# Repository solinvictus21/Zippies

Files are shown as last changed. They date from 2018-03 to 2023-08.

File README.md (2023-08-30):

# Zippies

Zippies are a project developed to create tiny, open source robots capable of following predefined path routines at high velocity in tight coordination together.

Fully Assembled Zippy

This repository includes all the details you need to build and run a Zippy...

- A complete set of [3D models](BodyModels) created in [SketchUp](https://www.sketchup.com/) that are required to build the outer body of a Zippy. Each of these parts is intended to be printed on a 3D printer and has been exported to a set of [STL files](BodyModels/STL) for convenience.
- A [schematic](LighthouseCircuit) and [complete bill of materials]() for a circuit designed to sense IR signals from a single HTC Vive Lighthouse to enable highly accurate, sub-millimeter localized positioning and orientation. The circuit is built in [AutoDesk Eagle](https://www.autodesk.com/products/eagle/free-download) and the PCB is available for immediate purchase directly [from Osh Park]().
- A complete [list of the additional hardware required](Documentation/Hardware.md) to assemble a Zippy. 
- The [software](PlatformIO) required to enable your Zippy robot to follow any predefined path you wish to create. A sample path is included in the codebase for testing new Zippy builds.
- An [iPhone app](iOSClient) (work in progress) that will allow you to control the Zippy directly and aid in debugging over Bluetooth.
- A [path building app](Builder) (work in progress) using [Unity 3D]() designed to allow you to build and simulate routines for your Zippies to follow and, on supported platforms, allow you to upload them directly to the Zippy via Bluetooth LE for immediate testing.

See each of the links above for more details about each aspect of this project and feel free to contact me for any assistance you may need if you are interested in building your own Zippy.

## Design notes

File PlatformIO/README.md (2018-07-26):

# Zippies for TinyScreen+

The following is a BOM to build a Zippy...

1. 1x [TinyScreen+](https://tinycircuits.com/collections/processors/products/tinyscreenplus) Main processor board plus battery charger, battery connector, and 96x64 full-color OLED screen.
2. 1x [290mAh Lithium Ion Battery](https://tinycircuits.com/products/lithium-ion-polymer-battery-3-7v-290mah)
3. 2x [Micro Metal Gearmotors](https://www.pololu.com/product/2363) from Pololu.com.
4. 1x [Dual Motor Tinyshield](https://tinycircuits.com/products/dual-motor-tinyshield) to drive the motors.
5. 1x [Proto-Board Tinysheild](https://tinycircuits.com/collections/proto-boards/products/proto-board-tinyshield?variant=14984618887) Be sure to purchase the version with no top connector. It will get in the way of attaching the HTC Vive Lighthouse sensor circuit.
6. 1x [Bluetooth Low Energy Tinyshield](https://tinycircuits.com/collections/communication/products/bluetooth-low-energy-tinyshield) Optional. Provides communication with the iOS app, useful for debugging.

It's not a cheap project to start on. The above required components of the robot add up to ~$96, not including Bluetooth, and that's before the cost of a 3D printer and the tools required to solder together the circuit board for sensing the Lighthouse signal. This is admittedly not a project for the feint-hearted or anyone new to building robots, but it IS a project for anyone excited about doing something new.

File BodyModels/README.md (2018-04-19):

# Parts Required For Body Assembly

Nearly all parts required to build a Zippy are included in the 3D models in this repository, with a few minor additions noted below.

Body Parts

## 3D-Printed Items

The parts are all modeled using [SketchUp](https://www.sketchup.com/), inspected for 3D printing solidity with the [Solid Inspector² extension](https://extensions.sketchup.com/en/content/solid-inspector%C2%B2), and exported to STL files using [this excellent STL exporter extension](https://extensions.sketchup.com/en/content/sketchup-stl).

I then slice the STL files with [Ultimaker Cura](https://ultimaker.com/en/products/ultimaker-cura-software) and print them with ABS on a [Monoprice Select Mini V2](https://www.monoprice.com/product?p_id=21711) 3D printer, but other slicers, materials, and 3D printers should work just fine. I print all parts with a raft to prevent compression of the bottom layers of each part. You will likely need to adjust 3D print settings during slicing for some of the parts to ensure they print properly as noted for each part.

### Body Bottom (1x)

The container for the motors. It is separated from the rest of the body to ease the assembly process. Notable features include (1) a "pillow" on the bottom to prevent corners of the model from snagging on irregularities on the surface as it moves around, (2) annular snap fits on the top to attach it to the rest of the body, and (3) holes for the screws to firmly attach the motor.

I recommend printing this part with supports so that the bottom pillow forms cleanly, and after removing the raft and supports, finish the bottom with a bit of acetone to ensure a smooth surface.

### Body (1x)

The main/center portion of the body and the housing for the various circuit boards. Notable features include (1) four insets along the bottom to connect to the annular snap fits on the body bottom, (2) brackets inside near the front to keep the TinyScreen in place, (3) holes on the left side to allow access to the TinyScreen power switch and reset button, and (4) insets on the inside left and right to connect to the cantilever snap fits on the body top.

This part likely does not require printing with supports. The overhangs for the insets on the bottom are small enough that they should bridge perfectly fine during printing without supports.

### Body Top (1x)

As the name implies, this is the top that attaches to the body to fully enclose the Zippy. Notable features include (1) cantilever snap fits on either side to connect the body top to the body, (2) lugs on the back corners to ensure proper alignment with the body when attached, (3) two holes for the infrared sensors from the Lighthouse circuit, and (4) a hole for the USB port to allow reprogramming of the Zippy without requiring the top to be removed.

### Wheel Motor Gears (2x)

The gears which attach to the axles on the two motors. Note that the gear is actually modeled as a proper "involute gear" and that the center hole is D-shaped to ensure tight attachment to the motor axles.

I have been asked why I don't just attach the wheels directly to the motors and just let them be offset from each other on either side of the Zippy. That's a good question, and I did not do that for a good reason. The PID controllers in the software codebase used to control each wheel would have to account for the offset of each wheel from the diode sensors on the top of the Zippy, complicating the math required to do proper path-following. Having the wheels centered on either side eliminates this complexity, and...honestly...I think it just looks better this way.

### Wheels (2x)

The name is self-explanatory. The important thing to note about this part is that the axle of the wheel and the outer rim of the wheel must be printed together even though they are technically modeled as two separate parts. That's because the axle has two endcaps to hold the rim in place which are larger than the hole in the rim for the central rod of the axle, a rather ingenious idea that I stole from another wheel model I found while randomly browsing around Thingiverse. Once the part is printed and the raft is fully removed, the axle should be able to turn within the rim, allowing the wheel to rotate once attached to the body. I even recommend applying a small amount of a light oil-based lubricant to this part after it is printed and cleaned up, to ensure that the outer rim turns freely around the axle.

## Accessories

In addition to the 3D printed parts, you'll also require the following accessories to complete assembly.

- 4x [M1.6 x 3mm screws](https://www.amazon.com/gp/product/B071DXG8D4/ref=oh_aui_detailpage_o09_s00?ie=UTF8&psc=1) used to attach the motors firmly to the bottom of the body.
- 2x [5mm x 1.5mm O-Rings](https://www.amazon.com/gp/product/B0180EQC22/ref=oh_aui_search_detailpage?ie=UTF8&psc=1) used as the "tires" that attach to the 3D-printed wheels.

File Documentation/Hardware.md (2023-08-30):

# Zippy Parts

The following is a complete set of parts required to build and run a Zippy robot.

1. A full set of [3D printed body parts](../BodyModels)
2. 1x [TinyScreen+](https://tinycircuits.com/collections/processors/products/tinyscreenplus) Main processor board plus battery charger, battery connector, and 96x64 color OLED screen.
3. 1x [290mAh Lithium Ion Battery](https://tinycircuits.com/products/lithium-ion-polymer-battery-3-7v-290mah)
4. 1x [Dual Motor Tinyshield](https://tinycircuits.com/products/dual-motor-tinyshield)
5. 1x [Proto-Board Tinysheild](https://tinycircuits.com/collections/proto-boards/products/proto-board-tinyshield?variant=14984618887) Be sure to purchase the version with no top connector.
6. 1x [Bluetooth Low Energy Tinyshield](https://tinycircuits.com/collections/communication/products/bluetooth-low-energy-tinyshield)
7. 2x [Micro Metal Gearmotors](https://www.pololu.com/product/2363) from Pololu.com.
8. 1x [HTC Vive Lighthouse](https://www.vive.com/us/accessory/base-station)
9. 1x fully-assembled [Lighthouse Sensor Circuit](../LighthouseCircuit)

TODO
tires (O-rings)
male and female headers for connecting sensor circuit
wiring for connecting motors

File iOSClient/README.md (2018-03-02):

# iPhone Client for Zippies

Run this on your phone, and it will automatically find and connect to a nearby Zippy. It will eventually need an update to allow selecting which Zippy to connect to when multiple are found, but that's on the "to do" list and unlikely to be a short-term issue.

Note that the emulator does not support the Bluetooth Low Energy profile, so the app will only function on a real device, which means that you'll need a iPhone developer account ($100/year) to install it on your phone.

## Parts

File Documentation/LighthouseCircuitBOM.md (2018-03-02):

# Lighthouse Sensor Circuit

This circuit is designed to provide sensors that detect IR signals from the HTC Vive Lighthouse in order to provide localized positioning for the Zippy. The board layout is published on [Osh Park](https://oshpark.com/shared_projects/vZVPRIY6) for easy ordering. All you have to do is solder the components onto it. The BOM and links to Digikey components are provided below.

1. 2x [BP104-FASZ](https://www.digikey.com/product-detail/en/osram-opto-semiconductors-inc/BP-104-FAS-Z/475-1344-1-ND/1227850) These are the IR sensors, the eyes of the circuit
2. 1x [TLV2464ID](https://www.digikey.com/product-detail/en/texas-instruments/TLV2464ID/296-10608-5-ND/380874) The heart of the circuit: a fast and reliable quad op-amp from TI.
3. First phase: voltage divider.
  - 2x [27k resistors](https://www.digikey.com/product-detail/en/panasonic-electronic-components/ERJ-3EKF2702V/P27.0KHCT-ND/1746753)
  - 2x [100nF capacictors](https://www.digikey.com/product-detail/en/samsung-electro-mechanics/CL10B104JB8NNNC/1276-1033-1-ND/3889119)
4. Second phase: transimpedance amplification
  - 2x [2.2pF capacitcors](https://www.digikey.com/product-detail/en/samsung-electro-mechanics/CL10C2R2BB8NNNC/1276-1084-1-ND/3889170)
  - 4x [100k resistors](https://www.digikey.com/product-detail/en/panasonic-electronic-components/ERJ-PA3J104V/P100KBZCT-ND/5036238) Also used in fourth-phase inverting amplification.
5. Third phase: high-pass filter.
  - 2x [4.7nf capacitors](https://www.digikey.com/product-detail/en/samsung-electro-mechanics/CL10B472JB8NNNC/1276-2061-1-ND/3890147)
  - 2x [18k resistors](https://www.digikey.com/product-detail/en/panasonic-electronic-components/ERJ-3EKF1802V/P18.0KHCT-ND/1746738)
6. Fourth phase: inverting amplification
  - 2x [1k resistors](https://www.digikey.com/product-detail/en/panasonic-electronic-components/ERJ-PB3D1001V/P20283CT-ND/6214538)

The passives can be soldered onto the board in any orientation, but pay particular attention to the orientation of the op-amp and diodes. Schematic diagram follows below if you're not an Eagle user.

Lighthouse Sensor Schematic

This is essentially a mash-up and a doubling of the circuit I originally started with from [Alex Shtuchkin's project](https://github.com/ashtuchkin/vive-diy-position-sensor) and [another circuit](https://trmm.net/Lighthouse) tweeted about by Alan Yates along with [some lessons I've learned about op-amps](http://www.radio-electronics.com/info/circuits/opamp_non_inverting/op_amp_non-inverting.php) along the way and a LOT of experimentation. At this point, the circuit seems to be fairly reliable across the range of distances that I experiment with.

For the curious, it has been suggested that, if you only have one Lighthouse, you must have three sensors to determine orientation along a 2D plane. Not true, actually. To do it with only two sensors on a robot that does not move in the up/down direction (assuming your sensors are equally-spaced on either side of the robot like this one), then you can just cross the vector between the two sensors with the down vector (0,0,-1) to get the orientation.

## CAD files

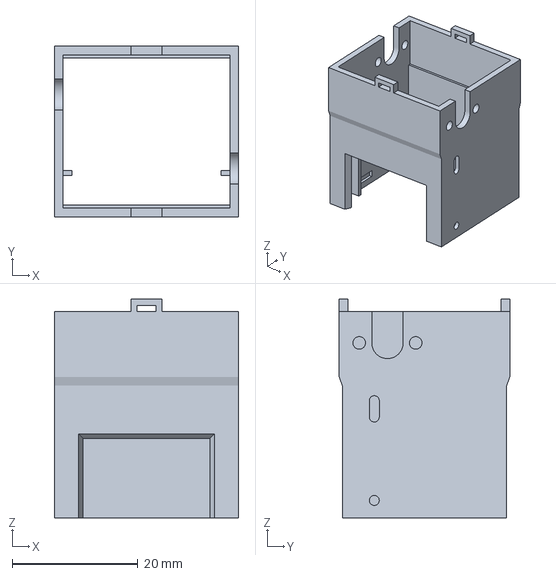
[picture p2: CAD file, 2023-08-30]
BodyModels/Body Middle - Experimental.3mf
29.4 x 27.2 x 34.9 mm

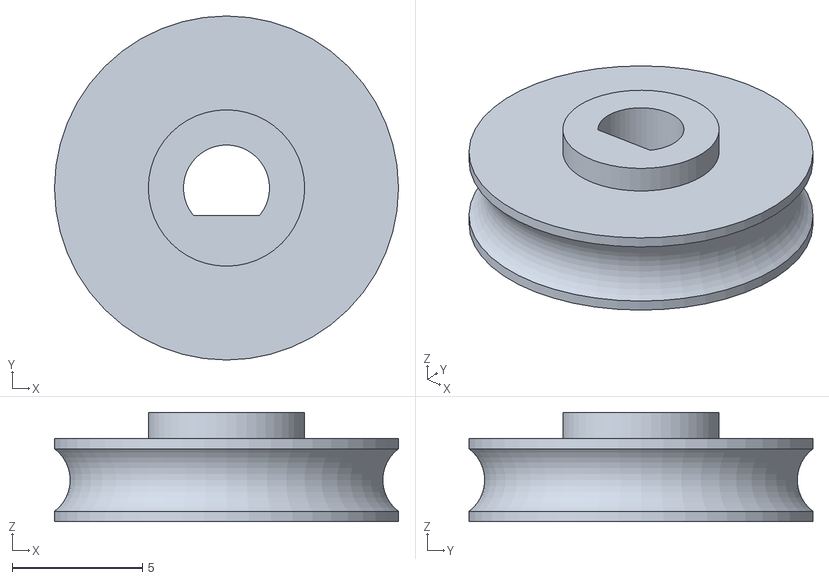
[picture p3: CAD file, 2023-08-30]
BodyModels/STL/Wheel.stl
13.2 x 13.2 x 4.20

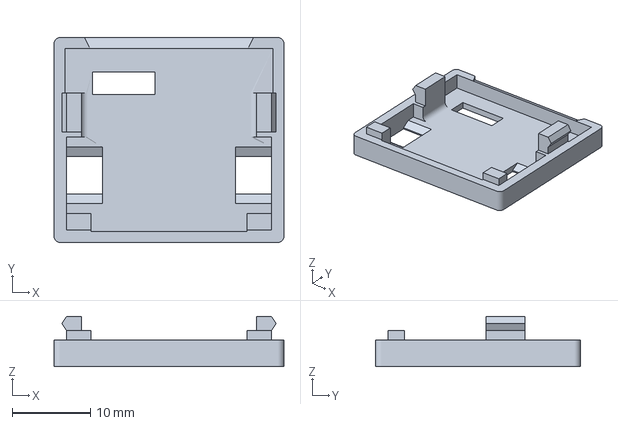
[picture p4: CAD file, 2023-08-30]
BodyModels/Body Top.3mf
29.4 x 26.2 x 6.40 mm

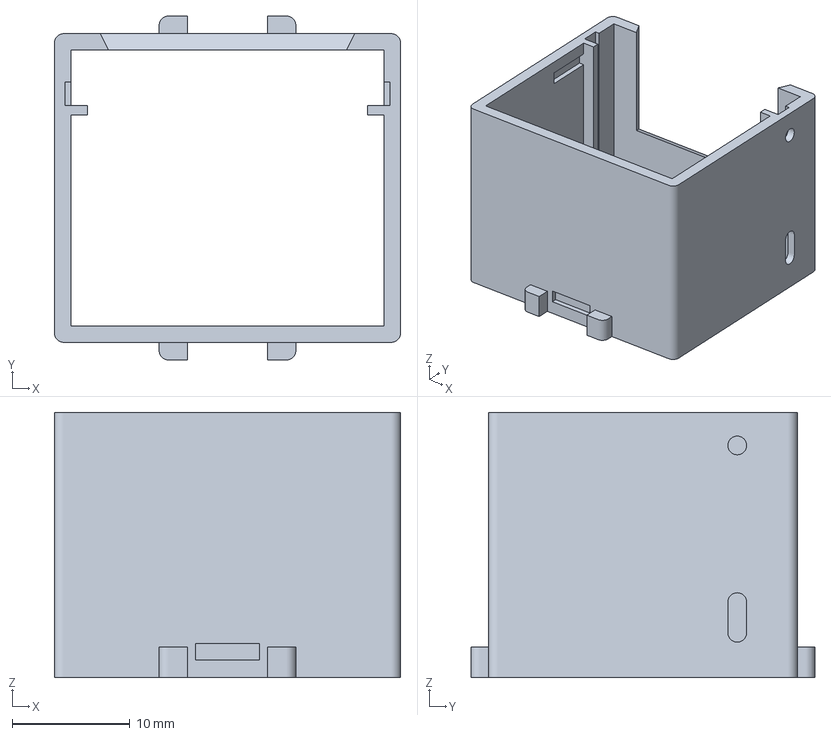
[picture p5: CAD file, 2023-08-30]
BodyModels/Body Middle.3mf
29.4 x 29.2 x 22.5 mm

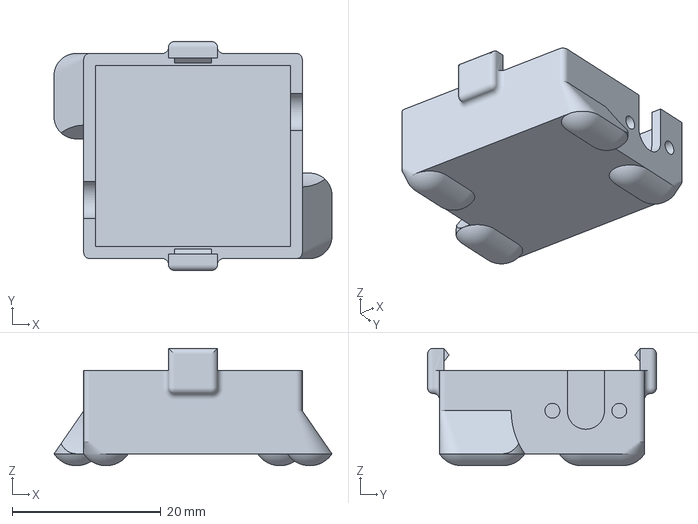
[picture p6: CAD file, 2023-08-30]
BodyModels/Body Bottom.3mf
37.4 x 30.8 x 15.8 mm

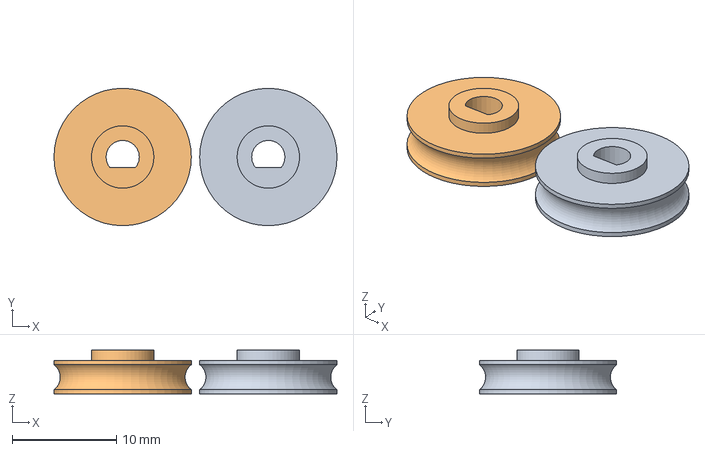
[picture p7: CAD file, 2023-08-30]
BodyModels/Wheels.3mf
27.2 x 13.2 x 4.20 mm

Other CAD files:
BodyModels/Body Parts.skp
BodyModels/Experimental Models.skp
BodyModels/Recharging Station.skp
BodyModels/STL/Body Bottom.stl
BodyModels/STL/Body Middle.stl
BodyModels/STL/Body Top.stl

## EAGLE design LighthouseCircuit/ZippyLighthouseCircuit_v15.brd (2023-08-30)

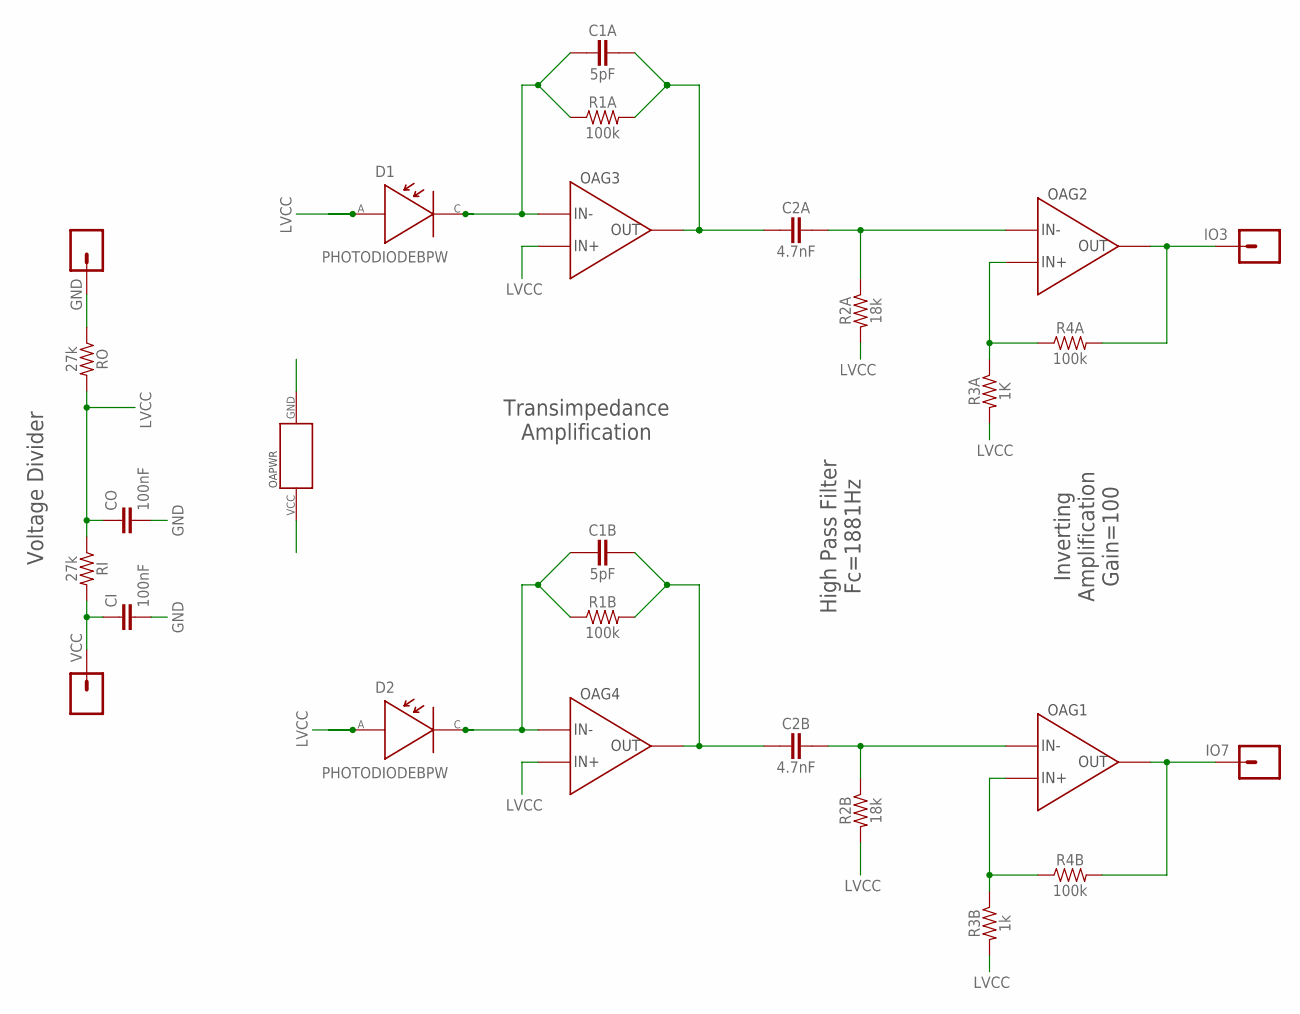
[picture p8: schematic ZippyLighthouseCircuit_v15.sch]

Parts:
C1A, C1B: 5pF; PASSIVE-0603
C2A, C2B: 4.7nF; PASSIVE-0603
CI: 100nF; 0603
CO: 100nF; 0603
D1, D2: PHOTODIODEBPW; BPW34_BP104_SMD
GND: CONN_01PTH_NO_SILK_YES_STOP; 1X01_NO_SILK
IO3, IO7: CONN_01PTH_NO_SILK_YES_STOP; 1X01_NO_SILK
OA: TLV2464IDM; D14-M
R1A, R1B, R4A, R4B: 100k; PASSIVE-0603
R2A, R2B: 18k; PASSIVE-0603
R3A: 1K; PASSIVE-0603
R3B: 1k; PASSIVE-0603
RI: 27k; 0603
RO: 27k; 0603
VCC: CONN_01PTH_NO_SILK_YES_STOP; 1X01_NO_SILK

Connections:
D1IN: C1B.1, D2.CATHODE, OA.13 (IN-), R1B.1
D1OA2P: C2B.2, OA.2 (IN-), R2B.1
D1OAOUT1: C1B.2, C2B.1, OA.14 (OUT), R1B.2
D2IN: C1A.1, D1.CATHODE, OA.9 (IN-), R1A.1
D2OA1OUT: C1A.2, C2A.1, OA.8 (OUT), R1A.2
D2OA2N: OA.5 (IN+), R3A.1, R4A.1
D2OA2P: C2A.2, OA.6 (IN-), R2A.1
GND: CI.2, CO.2, GND.1, OA.11 (GND), RO.1
IO3: IO3.1, OA.7 (OUT), R4A.2
IO7: IO7.1, OA.1 (OUT), R4B.2
LVCC: CO.1, D1.ANODE, D2.ANODE, OA.10 (IN+), OA.12 (IN+), R2A.2, R2B.2, R3A.2, R3B.2, RI.1, RO.2
unnamed: OA.3 (IN+), R3B.1, R4B.1
VCC: CI.1, OA.4 (VCC), RI.2, VCC.1

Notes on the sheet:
Voltage Divider
High Pass Filter Fc=1881Hz
Transimpedance Amplification
Inverting Amplification Gain=100

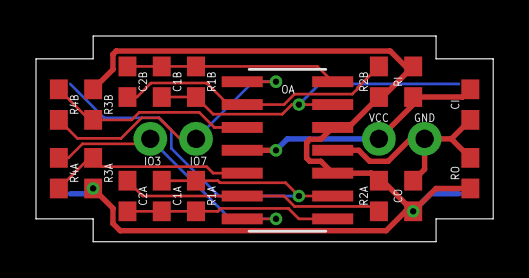
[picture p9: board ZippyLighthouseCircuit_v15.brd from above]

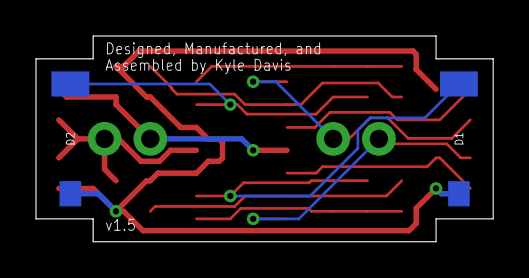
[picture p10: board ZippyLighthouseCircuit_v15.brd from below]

Board: 2 copper layers, 25.4 x 11.4 mm, 23 parts (2 on the bottom side), 13 nets.

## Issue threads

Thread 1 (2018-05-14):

Some questions.

modulab, 2018-05-14:
Hi,
I have't got the hardware yet but i'm planing to. I have a few questions for you.
Why did you use this MCU? Have you researched other options too?
How precise is the positioning at 48Mhz?
What is the current speed of the robot?
Awesome work !

solinvictus21, 2018-05-15:
Edit: Second attempt. My first attempt to respond to your email with an
attached video showing the speed of the Zippy moving about on the floor
failed because your email server rejected it for size. I'll try to get the
video uploaded to YouTube as additional info, but resending the rest of the
email without the attachment for now...

Hi! You are the first person to express interest in building a Zippy, so I
definitely want to help you in any way I can. To answer your questions in
short form, (a) it was just the fastest path to my end goal, (b) lots of
them, but I have research many options and am always looking for more, (c)
less than half a mm at distances of 1-5 meters from the Lighthouse, and (d)
about 600-800mm/sec. The lower speed during turns and the faster on
straightaways. I attached a relevant video to show him in motion.

For the longer answers, I've provided more detail below...

(a) I used this MCU strictly because it appeared to be the fastest path to
my goal, but I'm open to suggestions for other MCUs. While I was
experimenting with the Lighthouse sensor circuit, I actually implemented
early versions of the software first on the Arduino Uno and then the Teensy
3.2 platform. Based on your question, I'm guessing you're probably already
aware that there are basically two categories of MCUs: 8-bit and 32-bit.
And the latter is obviously significantly more capable than the former. I'm
a software developer by trade, and I actually didn't realize when I started
this project that there was such a big performance gap in the choice of
MCUs for robotics projects. I've since begun to favor Cortex-based
processors (although ESP32 is an interesting platform as well, mostly for
the WiFi integration), and the SAMD21-G18A variant built into the
TinyScreen+ was able to provide timings that matched up with the research
I've done to understand the timings of the Lighthouse..

(b) I've researched LOTS of other options, but I'm always open to others.
Caveat: I'm not a hardware engineer. I've only learned how to solder by
hand down to about 50 mils, which limits my ability to design circuit
boards using components that I'd otherwise prefer to integrate together
into a custom PCB for this project.

(c) I actually have a related codebase that I use to research exactly this
question, and all testing I've done is based on that codebase. If you build
one (and I'll put together some YouTube assembly videos to help if you do),
then you will be able to confirm the same data.

(d) The iPhone app that integrates with the Bluetooth connection will
display the information confirming these speeds as well. I'm still tuning
the PID controllers, though, so I may be able to get significantly faster
speeds in the future as well.

Just let me know if you have any more questions.

Kyle

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

solinvictus21, 2018-05-15:
YouTube video of one moving around a predefined path on the floor based on
positioning info from the Lighthouse.

https://www.youtube.com/edit?o=U&video_id=sSDTUJjHLLc

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

lgbeno, 2018-05-15:
Hey Kyle & Modulab,

Cool discussion here, glad to see interest in this area!  I can chime in a little bit on MCU selection because I've researched it quite a lot and have implemented the low level lighthouse stuff on a few MCUs (SAMD21 included).

I would say that SAMD21 is a pretty good choice for this application.  Mostly because the Arduino support is excellent and that makes adaptation easier for a larger population of people.  Most important to the application is availability of a >=24bit or larger timer capture that can be clocked at 48MHz or higher.  SAMD21 has this!  It is the most difficult processor by far to configure the timer properly but Kyle, looks like you have already gone through that pain.

Other processors that I've used are ST STM32F415 and NXP 54114.  The main reason for jumping to a chip like this is to get a faster clock rate and hardware floating point but in the process, you sacrifice the convenience of Arduino.

STM32F415 is quite the beast but also much more costly and physically much larger than the other options.

I think that the Teensy processors are also capable of hardware pulse capture so they are probably the best compromise of a faster ARM processor that also includes Floating point and is very maker friendly.

With that said I think SAMD21 is still an excellent choice with all things considered.

Unfortunately ESP8266 does not seem to have the proper timer capture functionality, some other peripherals can be hacked to serve the function but require constant CPU intervention.  I have not researched ESP32 in length but I think that it is very similar in this regard.

With a lot of research, I can say that I have yet to find a Radio System on Chip supporting all of these requirements which is unfortunate.

-Luke

solinvictus21, 2018-05-16:
> ... but Kyle, looks like you have already gone through that pain.

And indeed, it was painful. :) Programming at the AVR layer instead of using the Arduino APIs required reading and understanding a lot of different sections of the SAMD21 datasheet and a LOT of trial-and-error, but it's working great now. Still some optimizations I'd like to eventually add, such as using DMA to collect the pulse edge timing instead of software interrupts, and there seems to be some drift DFLL clock in the SAMD21 that I want to figure out how to tighten up. But before I tackle those, I want to make sure that SAMD21 is the platform I'll be sticking with for a while, particularly since ESP32 has caught my eye.

I actually started with Teensy 3.2, and I have quite a bit of the AVR-level code written to capture the Lighthouse edges on that platform as well, but it's not currently checked into the GitHub repository because the codebase on the whole is really quite stale at this point compared to the TinyScreen codebase. It wouldn't take much to move back in the future if I decided to go there again.

I figured the ESP8266 (and ATMega328P in the original Arduino) was probably too under-powered to get perform timings at the level that one needs for Lighthouse processing. I actually did some initial experimentation on the original Arduino before discovering this, though when I last looked back at it, I managed to home in on better timings than I would have expected for the processor speed it has available. Still, it eventually become another version of the codebase that has since been abandoned for exactly the reasons you describe.

But as far as the ESP32 platform, I understand that it actually quite capable and is comparable to (or even better than) the leap from the ATMega328P to SAMD21 in terms of sheer processing power. I am drawn to it as a possibility simply for the possibility of replacing the Bluetooth communication I'm currently doing, which is really only point-to-point, for the WiFi capabilities built into the ESP32 platform, which would allow me to do broadcast communication via UDP packets. That's something I will eventually need as I move toward trying to get multiple Zippies to move around in tight coordination together.

If I stick with SAMD21 instead of moving to ESP32, I'll also have to figure out the radio-system-on-a-chip issue(nrf24l01 currently has my eye) as well as how to hand solder down to smaller sizes, since they're all pretty tiny. Sounds like you have some good experience with this stuff, if you have any insight into how to make soldering tinier components easier, I'm all ears. :)

Regards,
Kyle

lgbeno, 2018-05-17:
Haha, yes, sorry I needed to laugh out loud about the timer stuff because it is almost not documented at all in the datasheet.  You probably used some Arduino forum reference code from some very nice people who also helped me read between the lines of those documents!

The DMA work was significantly and I have some ref code for that.  I based it off of an ADC example and now that you understand the event system better, this is just an extension of that knowledge.
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
solinvictus21, 2018-05-19:
@modulab

Sorry about the faulty YouTube link. This one should work for you…

https://www.youtube.com/watch?v=sSDTUJjHLLc

I just caught up on your post. You are in *exactly* the same place I was several months back. I am more than happy to help you out.

First of all, let me start by saying that I’m ultimately developing a “swarm” platform as well. I want to get to the point that I can build several Zippies that can do their own independent path-following while knowing exactly where they are and avoiding each other. To accomplish this, there is definitely a lot more to consider besides just the MCU. Specifically, you’ll need 4 additional pieces of functionality to think about when choosing a platform: battery recharging, wireless communication, motor drivers, and lighthouse sensors. Whichever platform you choose, you will also need to solve those 4 other problems to build out a swarm platform. Please take a couple of pieces of advice from the knowledge I gained from many months of failures I experienced at the beginning of this project.

- Use a 3D printer to make your robot body. This has been endlessly useful in allowing me to iterate on design changes quickly. I can provide recommendations for inexpensive 3D printers if you want them.

- Use metal gear motors, at least while you’re in the initial stages of building out the software. Un-geared DC motors have such a low torque and high RPM that error rates in movement are a nightmare. Plastic gear motors just end up in the garbage every few weeks. The extra space required for metal gear motors is worth the payoff in reliability and movement consistency. I recommend the gear motors I’m currently using for Zippies for a reliable motor that has consistent movement, but whatever motors you choose, stick with something between 500-2000RPM. No faster. You can always move to smaller and/or faster motors later. Of course, stepper motors and continuous servo motors are an option as well, but those are much slower, much larger, and are designed to provide a kind of closed-loop control that you are trying to implement using the Lighthouse instead, so why bother?

If you’re building out your own PCB, which it sounds like you might be doing, I highly recommend the SAMD21. It has a timer clock that you can use that is 48MHz, which is exactly the same as the timer clock in the Lighthouse. Plus it has the ability to capture timings in hardware, which is much more accurate compared to trying to capture timings based on a software interrupt. Timing is crucial when a handful of clock ticks can result in a difference of several centimeters in your estimated position. And if you choose the SAMD21, I will be able to provide better guidance with code samples and such while you’re trying to build the software to calculate position. Regardless of which platform you choose, though, let me know how your project progresses, and I’ll be more than happy to assist with any info that I can, since it sounds like we’re both pursuing a similar path.

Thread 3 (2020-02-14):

Having trouble to get the board to run error: "Ignoring signal echo: 5410 13563 26 5464 24463"

bbroecker, 2020-02-14:
Hi @solinvictus21,

I really like your project and I tried to make it run, but I'm running into problems.
I build the board with the specifications (resistors/capasitors) mentioned on the Readme.md from the
feature/MovementPlanningSupport branch.
The SensorFusor::loop always returns false,

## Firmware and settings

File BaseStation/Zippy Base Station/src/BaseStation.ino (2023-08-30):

#include "zippies/basestation/BaseStationController.h"

BaseStationController baseStationController;

void setup()
{
  SerialUSB.begin(115200);
  while (!SerialUSB);
  SerialUSB.println("Started serial communication.");

  baseStationController.start();
}

void loop()
{
  baseStationController.loop();
}

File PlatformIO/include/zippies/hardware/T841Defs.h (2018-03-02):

/*
T841Defs.h - Last modified 30 July 2015

These are register definitions for the ATTiny841, generated from files
included in the AVR-GCC project.

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
Written by Ben Rose for TinyCircuits.

The latest version of this library can be found at https://tiny-circuits.com/
*/

//Registers and associated bit numbers

#define T841_ADCSRB  0x20+0x04
#define T841_ADTS0   0
#define T841_ADTS1   1
#define T841_ADTS2   2
#define T841_ADLAR   3

#define T841_ADCSRA  0x20+0x05
#define T841_ADPS0   0
#define T841_ADPS1   1
#define T841_ADPS2   2
#define T841_ADIE    3
#define T841_ADIF    4
#define T841_ADATE   5
#define T841_ADSC    6
#define T841_ADEN    7

#define T841_ADCL    0x20+0x06
#define T841_ADCH    0x20+0x07

#define T841_ADMUXB  0x20+0x08
#define T841_GSEL0   0
#define T841_GSEL1   1
#define T841_REFS0   5
#define T841_REFS1   6
#define T841_REFS2   7

#define T841_ADMUXA  0x20+0x09
#define T841_MUX0    0
#define T841_MUX1    1
#define T841_MUX2    2
#define T841_MUX3    3
#define T841_MUX4    4
#define T841_MUX5    5

#define T841_ACSR0A  0x20+0x0A
#define T841_ACIS00  0
#define T841_ACIS01  1
#define T841_ACIC0   2
#define T841_ACIE0   3
#define T841_ACI0    4
#define T841_ACO0    5
#define T841_ACPMUX2 6
#define T841_ACD0    7

#define T841_ACSR0B  0x20+0x0B
#define T841_ACPMUX0 0
#define T841_ACPMUX1 1
#define T841_ACNMUX0 2
#define T841_ACNMUX1 3
#define T841_ACOE0   4
#define T841_HLEV0   6
#define T841_HSEL0   7

#define T841_ACSR1A  0x20+0x0C
#define T841_ACIS10  0
#define T841_ACIS11  1
#define T841_ACIC1   2
#define T841_ACIE1   3
#define T841_ACI1    4
#define T841_ACO1    5
#define T841_ACBG1   6
#define T841_ACD1    7

#define T841_ACSR1B  0x20+0x0D
#define T841_ACME1   2
#define T841_ACOE1   4
#define T841_HLEV1   6
#define T841_HSEL1   7

#define T841_TIFR1   0x20+0x0E
#define T841_TOV1    0
#define T841_OCF1A   1
#define T841_OCF1B   2
#define T841_ICF1    5

#define T841_TIMSK1  0x20+0x0F
#define T841_TOIE1   0
#define T841_OCIE1A  1
#define T841_OCIE1B  2
#define T841_ICIE1   5

#define T841_TIFR2   0x20+0x10
#define T841_TOV2    0
#define T841_OCF2A   1
#define T841_OCF2B   2
#define T841_ICF2    5

#define T841_TIMSK2  0x20+0x11
#define T841_TOIE2   0
#define T841_OCIE2A  1
#define T841_OCIE2B  2
#define T841_ICIE2   5

#define T841_PCMSK0  0x20+0x12

#define T841_GPIOR0  0x20+0x13

#define T841_GPIOR1  0x20+0x14

#define T841_GPIOR2  0x20+0x15

#define T841_PINB    0x20+0x16
#define T841_PINB3   3
#define T841_PINB2   2
#define T841_PINB1   1
#define T841_PINB0   0

#define T841_DDRB    0x20+0x17
#define T841_DDRB3   3
#define T841_DDRB2   2
#define T841_DDRB1   1
#define T841_DDRB0   0

#define T841_PORTB   0x20+0x18
#define T841_PORTB3  3
#define T841_PORTB2  2
#define T841_PORTB1  1
#define T841_PORTB0  0

#define T841_PINA    0x20+0x19
#define T841_PINA7   7
#define T841_PINA6   6
#define T841_PINA5   5
#define T841_PINA4   4
#define T841_PINA3   3
#define T841_PINA2   2
#define T841_PINA1   1
#define T841_PINA0   0

#define T841_DDRA    0x20+0x1A
#define T841_DDRA7   7
#define T841_DDRA6   6
#define T841_DDRA5   5
#define T841_DDRA4   4
#define T841_DDRA3   3
#define T841_DDRA2   2
#define T841_DDRA1   1
#define T841_DDRA0   0

#define T841_PORTA   0x20+0x1B
#define T841_PORTA7  7
#define T841_PORTA6  6
#define T841_PORTA5  5
#define T841_PORTA4  4
#define T841_PORTA3  3
#define T841_PORTA2  2
#define T841_PORTA1  1
#define T841_PORTA0  0

#define T841_EECR    0x20+0x1C
#define T841_EERE    0
#define T841_EEPE    1
#define T841_EEMPE   2
#define T841_EERIE   3
#define T841_EEPM0   4
#define T841_EEPM1   5

#define T841_EEDR    0x20+0x1D

#define T841_EEARL   0x20+0x1E
#define T841_EEARH   0x20+0x1F

#define T841_PCMSK1  0x20+0x20

#define T841_WDTCSR  0x20+0x21
#define T841_WDE     3
#define T841_WDP0    0
#define T841_WDP1    1
#define T841_WDP2    2
#define T841_WDP3    5
#define T841_WDIE    6
#define T841_WDIF    7

#define T841_TCCR1C  0x20+0x22
#define T841_FOC1B   6
#define T841_FOC1A   7

#define T841_GTCCR   0x20+0x23
#define T841_PSR     0
#define T841_TSM     7

#define T841_ICR1L   0x20+0x24
#define T841_ICR1H   0x20+0x25

// Reserved [0x26..0x27]

#define T841_OCR1BL  0x20+0x28
#define T841_OCR1BH  0x20+0x29

#define T841_OCR1AL  0x20+0x2A
#define T841_OCR1AH  0x20+0x2B

#define T841_TCNT1L  0x20+0x2C
#define T841_TCNT1H  0x20+0x2D

#define T841_TCCR1B  0x20+0x2E
#define T841_CS10    0
#define T841_CS11    1
#define T841_CS12    2
#define T841_WGM12   3
#define T841_WGM13   4
#define T841_ICES1   6
#define T841_ICNC1   7

#define T841_TCCR1A  0x20+0x2F
#define T841_WGM10   0
#define T841_WGM11   1
#define T841_COM1B0  4
#define T841_COM1B1  5
#define T841_COM1A0  6
#define T841_COM1A1  7

#define T841_TCCR0A  0x20+0x30
#define T841_WGM00   0
#define T841_WGM01   1
#define T841_COM0B0  4
#define T841_COM0B1  5
#define T841_COM0A0  6
#define T841_COM0A1  7

// Reserved [0x31]

#define T841_TCNT0   0x20+0x32
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

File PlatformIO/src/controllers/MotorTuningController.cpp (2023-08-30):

#include "zippies/controllers/MotorTuningController.h"
#include "zippies/config/BodyConfig.h"

#define DEFAULT_TEST_TIME 1000
#define DEFAULT_MOTOR_POWER_DELTA 100.0
#define DEFAULT_ACCEPT_STRAIGHT_MOTION 200.0
// #define TEST_START_MOTOR_LEFT 7200.0
// #define TEST_START_MOTOR_RIGHT 9100.0
#define TEST_START_MOTOR_LEFT 6800.0
#define TEST_START_MOTOR_RIGHT 8800.0
#define TEST_SLOW_MOTION_THRESHOLD 100.0
#define EPSILON_LINEAR 1.0
#define EPSILON_ANGULAR 0.052359877559830

//power differential on orange is 9143 and 7156 = 0.121909319590159

MotorTuningController::MotorTuningController(SensorFusor* s)
  : sensors(s)
{
    leftMotorPower = TEST_START_MOTOR_LEFT;
    rightMotorPower = TEST_START_MOTOR_RIGHT;
}

void MotorTuningController::resetTest()
{
    testStartingPosition.set(sensors->getPosition());
    motors.setMotorsDirect(leftMotorPower, rightMotorPower);
    testTimer = DEFAULT_TEST_TIME;
}

void MotorTuningController::start()
{
    deltaPosition.reset();
    linearVelocity = 0.0;
    turnRadius = 0.0;
    powerDifferential = 0.0;
    testComplete = false;
    resetTest();

    display.clearScreen();
    displayMetrics();
    display.displayText(0, 5 * display.getFontHeight(), "STARTED");
}

bool MotorTuningController::loop(unsigned long deltaTime)
{
    if (testComplete)
        return true;

    if (deltaTime < testTimer) {
        testTimer -= deltaTime;
        return true;
    }
    testTimer = DEFAULT_TEST_TIME;
    display.displayText(0, 5 * display.getFontHeight(), "TESTING");

    //evaluate our motion during the previous test
    calculateMetrics();
    displayMetrics();

    if (ensureTestableMotion()) {
        switch(currentTestState) {
            case MotorTuningTestState::PowerDifferential:
                testPowerDifferential();
                break;
            case MotorTuningTestState::Stiction:
                testStiction();
                break;
            case MotorTuningTestState::MinimumStraightSpeed:
                testMinimumStraightSpeed();
                break;
        }
    }

    return true;
}

bool MotorTuningController::ensureTestableMotion()
{
    //check if we're in motion
    if (deltaPosition.position.getD() < EPSILON_LINEAR) {
        //we're not moving at all; ramp up the power on both wheels
        leftMotorPower += DEFAULT_MOTOR_POWER_DELTA;
        rightMotorPower += DEFAULT_MOTOR_POWER_DELTA;
        resetTest();
        return false;
    }

    //check if we're turning
    double turn = deltaPosition.orientation.get();
    if (fabs(turn) >= EPSILON_ANGULAR) {
        //attempt to straighten our motion
        double powerDifference = 2.0 * powerDifferential * (leftMotorPower + rightMotorPower);
        leftMotorPower -= powerDifference;
        rightMotorPower += powerDifference;
        resetTest();
        return false;
    }

    return true;
}

void MotorTuningController::testPowerDifferential()
{
    //continue moving long enough to prove that we're moving straight
    if (deltaPosition.position.getD() > DEFAULT_ACCEPT_STRAIGHT_MOTION) {
        motors.stopMotors();
        testComplete = true;
        display.displayText(0, 5 * display.getFontHeight(), "DIFF DONE");
    }
}

void MotorTuningController::testStiction()
{
    //now that we're moving straight, test how slow we can go
    if (deltaPosition.position.getD() > TEST_SLOW_MOTION_THRESHOLD) {
        leftMotorPower -= 5.0 * DEFAULT_MOTOR_POWER_DELTA;
        rightMotorPower -= 5.0 * DEFAULT_MOTOR_POWER_DELTA;
        resetTest();
        return;
    }

    motors.stopMotors();
    testComplete = true;
    display.displayText(0, 5 * display.getFontHeight(), "STIC DONE");
}

void MotorTuningController::testMinimumStraightSpeed()
{
}

void MotorTuningController::calculateMetrics()
{
    const ZMatrix2* currentPosition = sensors->getPosition();
    deltaPosition.set(currentPosition);
    deltaPosition.unconcatFrom(&testStartingPosition);

    double angularVelocity = deltaPosition.position.atan();
    if (angularVelocity == 0.0) {
        linearVelocity = deltaPosition.position.getY();
        turnRadius = 0.0;
        return;
    }

    linearVelocity =
        (deltaPosition.position.getD() * angularVelocity) /
        sin(angularVelocity);
    turnRadius = linearVelocity / angularVelocity;

    powerDifferential = 1.0 -
            ((fabs(turnRadius) - WHEEL_CENTER_BODY_CENTER_OFFSET) /
            (fabs(turnRadius) + WHEEL_CENTER_BODY_CENTER_OFFSET));
    if (turnRadius < 0.0)
        powerDifferential = -powerDifferential;
}

void MotorTuningController::displayMetrics()
{
    uint8_t y = 0;
    display.displayLabelAndData(0, 0, "R", (int)rightMotorPower);
    display.displayLabelAndData(SCREEN_WIDTH_PIXELS_2, 0, "L", (int)leftMotorPower);

    y += display.getFontHeight();
    display.displayLabelAndData(0, y, "D", deltaPosition.position.getD());
    display.displayLabelAndData(SCREEN_WIDTH_PIXELS_2, y, "O", RAD2DEG * deltaPosition.orientation.get());

    y += display.getFontHeight();
    display.displayLabelAndData(0, y, "V", (int)linearVelocity);
    display.displayLabelAndData(SCREEN_WIDTH_PIXELS_2, y, "R", (int)turnRadius);

    y += display.getFontHeight();
    display.displayLabelAndData(0, y, "P", 100.0 * powerDifferential);
}

void MotorTuningController::stop()
{
    motors.stopMotors();
    if (!testComplete)
        display.displayText(0, 5 * display.getFontHeight(), "STOPPED");
}

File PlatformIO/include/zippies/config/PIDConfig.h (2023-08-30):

#ifndef _PIDCONFIG_H_
#define _PIDCONFIG_H_

#define PID_OUTPUT_LIMIT                   60000.0

//PID CONFIGURATION
#define PID_KP                               300.0
#define PID_KI                                 0.0
#define PID_KD                                22.0

#endif

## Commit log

2018-03-02 Added 3D models for body assembly.
    [Body Bottom.skp, Body Top.skp, Body.skp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]
2018-03-02 Added schematic and board layout for HTC Vive Lighthouse circuit.
    [Horizontally_Mounted_Lighthouse.brd, Horizontally_Mounted_Lighthouse.sch]
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2018-03-05 Renamed Arduino project to remove '+' symbol. Updated PID controller to be a little more accurate.
    [Horizontally_Mounted_Lighthouse.brd, Horizontally_Mounted_Lighthouse.sch]
2018-04-04 Preparing for minor Lighthouse tracking refactor.
    [ExenMiniShield.brd, ExenMiniShield.sch]
2018-04-18 Now have a working PID model. Refactoring MoveTowardPoint into FollowPath to accept multiple points.
2018-04-19 Finally got the PID control ironed out. They will now smoothly follow a demo elliptical path in area of about 2 meters across and 1.5 meters in depth all on their own.
    [ExenMiniShield.brd]
2018-05-04 Modified 3D body models to use offset, direct-drive wheels because the gears were too small to be printed accurately enough to prevent binding and other movement errors that prevented accurate self-n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
    [ExenMiniShield.brd]
2018-05-08 As the self-driving control model has become more refined, I've been able to push the Zippies faster. Now set at a max velocity of 800mm/s.
2018-05-09 Further refined the driving model and improved the position data by incorporating factory calibration data into the position calculation based on code and documentation from the libsurvive project. T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
2018-05-24 Significantly stabilized the acceleration from full stop by slowing down the maximum speed. There is a physical limitation preventing them from accelerating any faster from full stop. Now that their 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
    [ExenMiniBatteryShield.brd, ExenMiniBatteryShield.sch, ExenMiniShield.brd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]
2018-05-30 Moved to separate PID configuration for each wheel. Since the left wheel is offset toward the rear and the right wheel is offset toward the front, the left wheel needs to be less aggressive or the Zi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
    [ExenMiniLighthouseShield.brd, ExenMiniLighthouseShield.sch, ExenMiniMotorShield.brd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]
2018-07-12 Reached a point where auto-drive mode is consistent and reliable.
    [Body Bottom.skp, Body Top.skp, Body.skp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]
2018-07-26 Path following is now very smooth. Zippies sync up on Lighthouse OOTX frame preamble (17 successive zero OOTX bits). Added config to modify behavior of different Zippies. Started work on using Blueto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
    [Body Bottom.skp]
2018-08-01 Zippies can now perform perfectly synchronous drive along any predefined path.
    [Body Bottom.skp, ExenMiniLighthouseShield.sch, ExenMiniShield.brd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]
2018-08-16 Tagged model in each SketckUp file that should be used as the current model to 3D print.
    [Body Bottom.skp, Body Top.skp, Body.skp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]
2018-08-17 Added an integrated motor/lighthouse circuit design and updated path following code to use bezier curves to make path following significantly smoother.
    [CenteredLighthouseCircuit.brd, CenteredLighthouseCircuit.sch, DiodeBoard.brd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]
2018-08-28 Working on creating individual commands and implementing arbitrary path-following of straight line segments as well as bezier curves.
    [MainBoard.brd, MainBoard.sch, RadioShield.brd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]
2018-10-02 Beginning to transition PID model from linear+angular velocity PIDs to independent PIDs for each wheel.
    [Body Bottom.skp, Body Top.skp, Body.skp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]
2018-11-08 Implemented two different models for kinematics. Experimenting with each to determine which is more reliable across the widest range of velocities.
    [Body Bottom.skp, Body Top.skp, Wheel.skp]
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2019-03-01 Significantly stabilized the position calculation and the new driving model with independent PIDs for each wheel.
    [Body Bottom.skp, Body Top.skp, Body.skp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]
2019-04-19 Progress toward using bi-arc computations for execution of path following.
    [Body Bottom.skp, Body Top.skp, Body.skp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]
2019-06-18 Added support for bi-arc movement, which can be more easily linearly interpolated than cubic bezier movement. Made several other architectural changes to streamline movement planning.
    [Body Top.skp, Body.skp, Wheel.skp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]
2019-06-27 Minor changed to SketchUp models.
    [Body Top.skp, Wheel.skp]
2019-08-23 Numerous improvements to movement algorithm, path planning, and dance routine execution.
    [Body Top.skp, Body.skp]
2019-11-01 Significantly refactored the sensor fusion to calculate updated positions in lock-step with the Lighthouse sweeps. New positions are now calculated only after both sensors have received a hit on both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
2019-11-26 Eliminated use of routine controller and simplified the model for defining paths while adding support for velocity easing for each path segment.
2019-12-27 Working on initial demo of multiple Zippies in coordination.
    [ExenMiniBatteryShield.brd, ExenMiniBatteryShield.sch, ExenMiniLighthouseShield.brd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]
2020-02-01 Made some huge strides in these changes. Nothing is quite as satisfying as deleting code, and I've deleted much code in this commit, because I've been able to develop a new path-following algorithm t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
    [Recharging Station.skp]
2020-04-08 Significant changes and refactored codebase layout. Improvements made to path following, PID control, path execution, added a new default path, and many other changes.
    [Body Bottom.skp, Body Parts.skp, Body Top.skp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]
2020-07-02 Switched path definitions to use monotonic hermite curves, allowing for significantly more sophisticated and flexible path planning.
    [Body Bottom.stl, Body Middle.stl, Body Parts.skp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]
2020-07-22 Working on a new path following implementation.
    [Body Bottom.3mf, Body Middle - Experimental.3mf, Body Middle.3mf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]
2020-12-09 Attempting to perfect path following controller code. Preparing to delete old path definition code.
    [Body Middle.3mf, Body Top.3mf]
2021-07-06 Switching to a kinematic movement model instead of using cubic beziers for path planning.
2021-11-30 Preparing to prune old code out of the codebase.
    [ZippyLighthouseCircuit_v17.brd, ZippyLighthouseCircuit_v17.sch]
2023-08-28 Ported over fixes and enhancements to driving algorithms from Webots simulation experiments. Added a motor tuning controller to begin work setting up tests to capture motor tuning parameters to bette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
    [BaseStationController.cpp, DrivingController.h]

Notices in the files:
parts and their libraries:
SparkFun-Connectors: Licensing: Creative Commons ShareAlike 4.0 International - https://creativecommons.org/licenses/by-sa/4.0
